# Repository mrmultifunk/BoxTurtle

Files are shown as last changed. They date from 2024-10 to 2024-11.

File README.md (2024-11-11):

# BoxTurtle V1.0
BoxTurtle Automated Filament Changer (requires AFC-Klipper-Add-On (Beta))

BT_Render
Join me on Discord (https://discord.gg/eT8zc3bvPR)

BoxTurtle is exactly what it appears to be — an open source AMS style filament changer for [Klipper](https://klipper3d.org) machines. 
BoxTurtle requires the AFC-Klipper Add-On (found [here](https://github.com/ArmoredTurtle/AFC-Klipper-Add-On)).
The goal of BoxTurtle is to deliver a user experience as close to an AMS as possible in vanilla Klipper. i.e. an "AMS" for any klipperized printer regardless of form factor but [VORON Design](https://vorondesign.com) printers in particular.

If you appreciate the work we are doing, you can support us [here](https://www.armoredturtle.com/pages/donate).

# How it works

BoxTurtle is an automated, lane-based filament changing system, also known by some as a "Type B MMU." Each lane is equipped with its own dedicated motor that moves filament to and from the tool head independently, eliminating the need for a selector cart or servos. Synchronization between the lane motor and the tool head occurs when the filament triggers a sensor (such as [FilaTector](https://github.com/ArmoredTurtle/Filatector)) that is located in or near the tool head.

To accommodate any differences in rotation distance between the extruder in the tool head and the lane motors, BoxTurtle uses a toolhead buffer, such as the [Belay by Annex Engineering](https://github.com/Annex-Engineering/Belay) or the [TurtleNeck](https://github.com/ArmoredTurtle/TurtleNeck) by ArmoredTurtle. This system is "bufferless," meaning no filament boxes (no spaghetti boxes) are required, similar to the AMS. Each lane features an independent respooler equipped with a brushed motor, which helps rewind the spool and assists the lane motor in feeding the filament smoothly. This prevents issues like spool tangling or "bucking."

For precise PWM control of the brushed motors, BoxTurtle relies on a custom MCU, AFC-lite, developed by [Isik's Tech @xbst](https://github.com/xbst/AFC-Lite/)  While the system currently supports BTT MMB CAN, this is a temporary solution to facilitate broader testing and will not be a permanent feature.

# Manual (WIP)

[Will update this as progress is made](https://armoredturtle.xyz)

# Wiring

BoxTurtle_AFC-Lite_Pinout

# Slicer configuration

[Orca Slicer](https://github.com/SoftFever/OrcaSlicer) is the preferred slicer for BoxTurtle use.
## Printer Settings
Orca_Pinter_Settings
## Material Settings
Orca_Material_Settings
## Ramming Settings
Orca_Matterial_Settings

## Printer Machine G-Code
```
M104 S0 ; Stops OS from sending temp waits separately
M140 S0
PRINT_START EXTRUDER=[nozzle_temperature_initial_layer] BED=[bed_temperature_initial_layer_single] Chamber=[chamber_temperature] PRINT_MIN={first_layer_print_min[0]},{first_layer_print_min[1]} PRINT_MAX={first_layer_print_max[0]},{first_layer_print_max[1]} TOOL={initial_tool}
```
## Change Filament G-Code
```
T[next_extruder]
```

## BoxTurtle sourcing/vendors
While BoxTurtle can be mostly self-sourced, some vendors offer partial or full BoxTurtle kits. These vendors also have dedicated channels on the Armored Turtle Discord.

US:
- [DLLPDF](https://dllpdf.com) sells a [BoxTurtle frame kit](http://dllpdf.com/box-turtle-frame)
- [Isik's Tech](https://store.isiks.tech/) has BOM parts, including full kits [here](https://store.isiks.tech/collections/box-turtle-parts). Isik's Tech also ships internationally.
- [Fabreeko](https://www.fabreeko.com/products/box-turtle?_pos=4&_psq=box&_ss=e&_v=1.0)
- [KB3D](https://kb-3d.com/store/boxturtle/2132-pre-order-ldo-box-turtle-automated-filament-changer-kit-v10.html)
- [West3D](https://west3d.com/products/box-turtle-automated-filament-changer-multi-material-unit-by-armored-turtle)
  
EU:
- [Alchemy3D.de](https://alchemy3d.de) has a [BOM in a box kit](https://alchemy3d.de/products/boxturtle)
- [Lab4450.com](https://lab4450.com) resells the [AFC-Lite MCU](https://lab4450.com/product/afc-lite-board/)
- [3DO](https://3do.dk/3d-printer/2942-ldo-boxturtle-afc-kit-til-klipper-printere-forudbestilling.html)

UK:
- [OneTwo3D.co.uk](https://www.onetwo3d.co.uk)
- [Desktop Machine Shop](https://www.desktopmachineshop.com/shop/ldo-boxturtle-afc-kit-v1-0-163?category=4#attribute_values=)
  
AU:
- [DREMC](https://store.dremc.com.au/products/ldo-box-turtle-hardware-kit)
  
## Merch
- BoxTurtle T-Shirt ($3 from each sale goes to support ArmoredTurtle) via [Cotton Bureau](https://cottonbureau.com/p/QKF5XC/shirt/colored-box-turtle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)- also has sweatshirt/hoodie variants
- BoxTurtle Sticker via [Dr. Mursey](https://drmursey.myshopify.com/products/box-turtle)

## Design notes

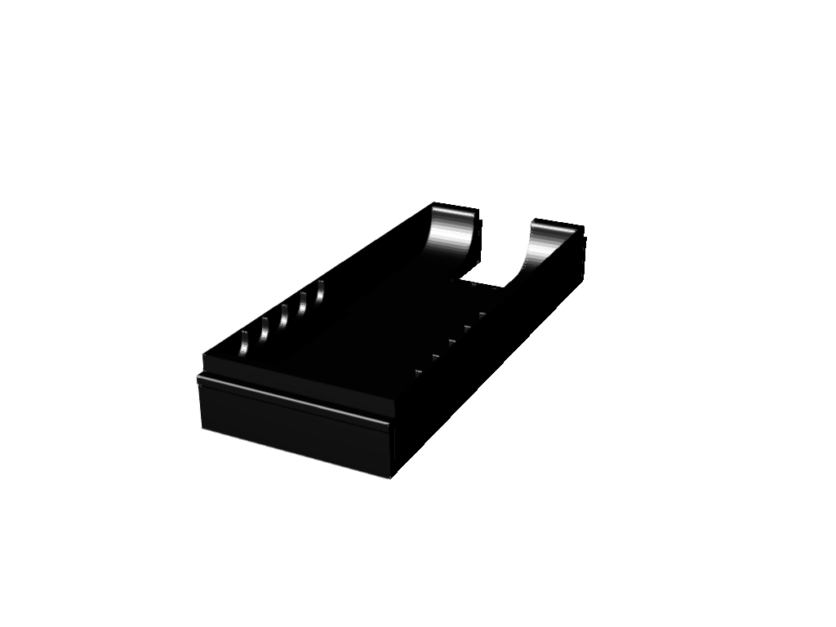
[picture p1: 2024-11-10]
Print_Checklist/images/BoxTurtle/STLs/Trays_(Print_4_of_your_choice)/No_Hardware/tray_plain.stl.png

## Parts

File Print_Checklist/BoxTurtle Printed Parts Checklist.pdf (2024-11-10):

# BoxTurtle Printed Parts Checklist

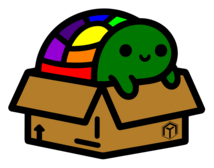
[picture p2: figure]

### Print all of these common parts

STL Preview | Filename | Quantity Needed

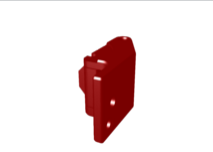
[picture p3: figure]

BoxTurtle/STLs/Extruder/
[a]_guidler_x4.stl (https://github.com/ArmoredTurtle/BoxTurtle/tree/main/STLs/Extruder/[a]_guidler_x4.stl) | 4 ☐☐☐☐

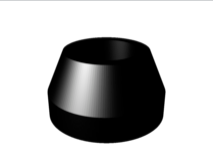
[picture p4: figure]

BoxTurtle/STLs/Frame/
foot_tpu_x4.stl (https://github.com/ArmoredTurtle/BoxTurtle/tree/main/STLs/Frame/foot_tpu_x4.stl) | 4 ☐☐☐☐

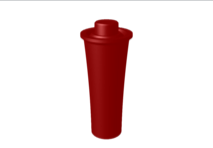
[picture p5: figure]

BoxTurtle/STLs/Idlers/
[a]_idler_roller_x8.stl (https://github.com/ArmoredTurtle/BoxTurtle/tree/main/STLs/Idlers/[a]_idler_roller_x8.stl)

8
☐☐☐☐☐☐☐☐

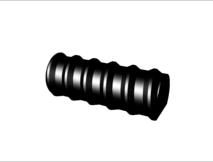
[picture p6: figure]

BoxTurtle/STLs/Idlers/ idler_threaded_joint_x4.stl (https://github.com/ArmoredTurtle/BoxTurtle/tree/main/STLs/Idlers/idler_threaded_joint_x4.stl) | 4 ☐☐☐☐

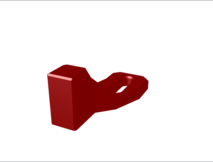
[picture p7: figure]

BoxTurtle/STLs/Respooler/ [a]_feed_trigger_retainer_x4.stl (https://github.com/ArmoredTurtle/BoxTurtle/tree/main/STLs/Respooler/[a]_feed_trigger_retainer_x4.stl) | 4 ☐☐☐☐

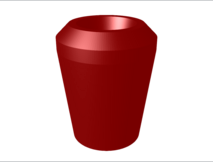
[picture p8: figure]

BoxTurtle/STLs/Respooler/ [a]_feeder_x4.stl (https://github.com/ArmoredTurtle/BoxTurtle/tree/main/STLs/Respooler/[a]_feeder_x4.stl) | 4 ☐☐☐☐
BoxTurtle/STLs/Respooler/ [a]_led_retainer_x4.stl (https://github.com/ArmoredTurtle/BoxTurtle/tree/main/STLs/Respooler/[a]_led_retainer_x4.stl) | 4 ☐☐☐☐
BoxTurtle/STLs/Respooler/ [a]_lightbox_x4.stl (https://github.com/ArmoredTurtle/BoxTurtle/tree/main/STLs/Respooler/[a]_lightbox_x4.stl) | 4 ☐☐☐☐

BoxTurtle/STLs/Respooler/ [a]_wheel_x8.stl (https://github.com/ArmoredTurtle/BoxTurtle/tree/main/STLs/Respooler/[a]_wheel_x8.stl) | 8 ☐☐☐☐☐☐☐☐
BoxTurtle/STLs/Respooler/ [c]_led_diffuser_x4.stl (https://github.com/ArmoredTurtle/BoxTurtle/tree/main/STLs/Respooler/[c]_led_diffuser_x4.stl) | 4 ☐☐☐☐
BoxTurtle/STLs/Respooler/ frame_left_x4.stl (https://github.com/ArmoredTurtle/BoxTurtle/tree/main/STLs/Respooler/frame_left_x4.stl) | 4 ☐☐☐☐
BoxTurtle/STLs/Respooler/ frame_right_x4.stl (https://github.com/ArmoredTurtle/BoxTurtle/tree/main/STLs/Respooler/frame_right_x4.stl) | 4 ☐☐☐☐
BoxTurtle/STLs/Respooler/ gearbox_cover_x4.stl (https://github.com/ArmoredTurtle/BoxTurtle/tree/main/STLs/Respooler/gearbox_cover_x4.stl) | 4 ☐☐☐☐

BoxTurtle/STLs/Respooler/ helical_gear_15_teeth_x4.stl (https://github.com/ArmoredTurtle/BoxTurtle/tree/main/STLs/Respooler/helical_gear_15_teeth_x4.stl) | 4 ☐☐☐☐
BoxTurtle/STLs/Respooler/ helical_gear_30_teeth_x4.stl (https://github.com/ArmoredTurtle/BoxTurtle/tree/main/STLs/Respooler/helical_gear_30_teeth_x4.stl) | 4 ☐☐☐☐
BoxTurtle/STLs/Respooler/ motor_mount_x4.stl (https://github.com/ArmoredTurtle/BoxTurtle/tree/main/STLs/Respooler/motor_mount_x4.stl) | 4 ☐☐☐☐
BoxTurtle/STLs/Respooler/ spur_gear_30_spacer_x4.stl (https://github.com/ArmoredTurtle/BoxTurtle/tree/main/STLs/Respooler/spur_gear_30_spacer_x4.stl) | 4 ☐☐☐☐
BoxTurtle/STLs/Respooler/ tpu_tire_x8.stl (https://github.com/ArmoredTurtle/BoxTurtle/tree/main/STLs/Respooler/tpu_tire_x8.stl) | 8 ☐☐☐☐☐☐☐☐

BoxTurtle/STLs/Respooler/ trigger_x4.stl (https://github.com/ArmoredTurtle/BoxTurtle/tree/main/STLs/Respooler/trigger_x4.stl) | 4 ☐☐☐☐
BoxTurtle/STLs/Skirts/ front_skirt_x2.stl (https://github.com/ArmoredTurtle/BoxTurtle/tree/main/STLs/Skirts/front_skirt_x2.stl) | 2 ☐☐
BoxTurtle/STLs/Skirts/ left_rear_skirt.stl (https://github.com/ArmoredTurtle/BoxTurtle/tree/main/STLs/Skirts/left_rear_skirt.stl) | 1 ☐
BoxTurtle/STLs/Skirts/ right_rear_skirt.stl (https://github.com/ArmoredTurtle/BoxTurtle/tree/main/STLs/Skirts/right_rear_skirt.stl) | 1 ☐

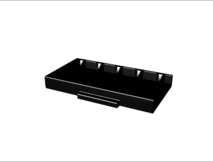
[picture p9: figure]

BoxTurtle/STLs/Skirts/ side_skirt_x4.stl (https://github.com/ArmoredTurtle/BoxTurtle/tree/main/STLs/Skirts/side_skirt_x4.stl) | 4 ☐☐☐☐

BoxTurtle/STLs/
Tools/15t_installation_tool.stl (https://github.com/ArmoredTurtle/BoxTurtle/tree/main/STLs/Tools/15t_installation_tool.stl) | 1 ☐

BoxTurtle/STLs/
Tools/30t_installation_tool.stl (https://github.com/ArmoredTurtle/BoxTurtle/tree/main/STLs/Tools/30t_installation_tool.stl) | 1 ☐

### Electronics Mount (choose one)

STL Preview | Filename | Quantity Needed

BoxTurtle/STLs/Electronics/
afc_mount.stl (https://github.com/ArmoredTurtle/BoxTurtle/tree/main/STLs/Electronics/afc_mount.stl) | 1 ☐

BoxTurtle/STLs/Electronics/
mmb_mount.stl (https://github.com/ArmoredTurtle/BoxTurtle/tree/main/STLs/Electronics/mmb_mount.stl) | 1 ☐

BoxTurtle/STLs/Electronics/
mosfetti_mount.stl (https://github.com/ArmoredTurtle/BoxTurtle/tree/main/STLs/Electronics/mosfetti_mount.stl) | 1 ☐

### Print ONE set of the below two sections, depending on switch type

D2HW-style switches + MR63ZZ bearings

STL Preview | Filename | Quantity Needed
| BoxTurtle/STLs/Extruder/ D2HW_Switch/ extruder_housing_x4.stl (https://github.com/ArmoredTurtle/BoxTurtle/tree/main/STLs/Extruder/D2HW_Switch/extruder_housing_x4.stl)
4 ☐☐☐☐

BoxTurtle/STLs/Extruder/
D2HW_Switch/motor_plate_x4.stl (https://github.com/ArmoredTurtle/BoxTurtle/tree/main/STLs/Extruder/D2HW_Switch/motor_plate_x4.stl) | 4 ☐☐☐☐

BoxTurtle/STLs/Skirts/
[a]_hub_D2HW.stl (if using a hub) (https://github.com/ArmoredTurtle/BoxTurtle/tree/main/STLs/Skirts/[a]_hub_D2HW.stl) | 1 ☐

D2F-style switches + 5mm ball bearings

STL Preview | Filename | Quantity Needed

BoxTurtle/STLs/Extruder/D2F_Switch/
[a]_microswitch_retainer_x4.stl (https://github.com/ArmoredTurtle/BoxTurtle/tree/main/STLs/Extruder/D2F_Switch/[a]_microswitch_retainer_x4.stl) | 4 ☐☐☐☐

BoxTurtle/STLs/Extruder/D2F_Switch/
extruder_housing_x4.stl (https://github.com/ArmoredTurtle/BoxTurtle/tree/main/STLs/Extruder/D2F_Switch/extruder_housing_x4.stl) | 4 ☐☐☐☐

BoxTurtle/STLs/Extruder/D2F_Switch/
motor_plate_x4.stl (https://github.com/ArmoredTurtle/BoxTurtle/tree/main/STLs/Extruder/D2F_Switch/motor_plate_x4.stl) | 4 ☐☐☐☐

BoxTurtle/STLs/Skirts/[a]_hub_D2F.stl
(if using a hub) (https://github.com/ArmoredTurtle/BoxTurtle/tree/main/STLs/Skirts/[a]_hub_D2F.stl) | 1 ☐

### Corners - print ONE set

Corners - Printed (with LEDs)

STL Preview | Filename | Quantity Needed


BoxTurtle/STLs/Frame/
Printed_Corners/[a]_foot_x4.stl (https://github.com/ArmoredTurtle/BoxTurtle/tree/main/STLs/Frame/Printed_Corners/[a]_foot_x4.stl) | 4 ☐☐☐☐

BoxTurtle/STLs/Frame/
Printed_Corners/
[o]_corner_diffuser_x4.stl (https://github.com/ArmoredTurtle/BoxTurtle/tree/main/STLs/Frame/Printed_Corners/[o]_corner_diffuser_x4.stl)

4 ☐☐☐☐

BoxTurtle/STLs/Frame/
Printed_Corners/corner_printed_x4.stl (https://github.com/ArmoredTurtle/BoxTurtle/tree/main/STLs/Frame/Printed_Corners/corner_printed_x4.stl) 4 ☐☐☐☐


BoxTurtle/STLs/Frame/
Printed_Corners/
led_corner_cover_x4.stl (https://github.com/ArmoredTurtle/BoxTurtle/tree/main/STLs/Frame/Printed_Corners/led_corner_cover_x4.stl)

4 ☐☐☐☐


BoxTurtle/STLs/Frame/
Printed_Corners/led_frame_x4.stl (https://github.com/ArmoredTurtle/BoxTurtle/tree/main/STLs/Frame/Printed_Corners/led_frame_x4.stl) | 4 ☐☐☐☐

Corners - Printed (no LEDs)

STL Preview | Filename | Quantity Needed

BoxTurtle/STLs/Frame/
Printed_Corners/[a]_foot_x4.stl (https://github.com/ArmoredTurtle/BoxTurtle/tree/main/STLs/Frame/Printed_Corners/[a]_foot_x4.stl) | 4 ☐☐☐☐

BoxTurtle/STLs/Frame/
Printed_Corners/corner_printed_x4.stl (https://github.com/ArmoredTurtle/BoxTurtle/tree/main/STLs/Frame/Printed_Corners/corner_printed_x4.stl) 4 ☐☐☐☐

BoxTurtle/STLs/Frame/
Printed_Corners/
solid_corner_cover_x4.stl (https://github.com/ArmoredTurtle/BoxTurtle/tree/main/STLs/Frame/Printed_Corners/solid_corner_cover_x4.stl)

4 ☐☐☐☐


100mm 2020 extrusions (uncommon)

STL Preview | Filename | Quantity Needed
| BoxTurtle/STLs/Frame/ Extrusion_Corners/ [a]_foot_extrusion_x4.stl (https://github.com/ArmoredTurtle/BoxTurtle/tree/main/STLs/Frame/Extrusion_Corners/[a]_foot_extrusion_x4.stl)
4 ☐☐☐☐

BoxTurtle/STLs/Frame/
Extrusion_Corners/
corner_cover_extrusion_x4.stl (https://github.com/ArmoredTurtle/BoxTurtle/tree/main/STLs/Frame/Extrusion_Corners/corner_cover_extrusion_x4.stl)

4 ☐☐☐☐

BoxTurtle/STLs/Frame/
Extrusion_Corners/
no_panel_spacer_extrusion_x4.stl (https://github.com/ArmoredTurtle/BoxTurtle/tree/main/STLs/Frame/Extrusion_Corners/no_panel_spacer_extrusion_x4.stl)

4 ☐☐☐☐


### Rear skirts (print one, hub or passthrough)

STL Preview | Filename | Quantity Needed

BoxTurtle/STLs/Skirts/
rear_skirt_center_hub.stl (https://github.com/ArmoredTurtle/BoxTurtle/tree/main/STLs/Skirts/rear_skirt_center_hub.stl) | 1 ☐

BoxTurtle/STLs/Skirts/
rear_skirt_center_passthrough.stl (https://github.com/ArmoredTurtle/BoxTurtle/tree/main/STLs/Skirts/rear_skirt_center_passthrough.stl) | 1 ☐

### Trays - No Hardware (235mm or larger build plates) - print one set (if build plate allows)

No Hardware - Desiccant

STL Preview | Filename | Quantity Needed
| BoxTurtle/STLs/ Trays_(Print_4_of_your_choice)/ No_Hardware/tray_desiccant.stl (https://github.com/ArmoredTurtle/BoxTurtle/tree/main/STLs/Trays_(Print_4_of_your_choice)/No_Hardware/tray_desiccant.stl)
4 ☐☐☐☐


No Hardware - Inlay

STL Preview | Filename | Quantity Needed
| BoxTurtle/STLs/ Trays_(Print_4_of_your_choice)/ No_Hardware/tray_inlay.stl (https://github.com/ArmoredTurtle/BoxTurtle/tree/main/STLs/Trays_(Print_4_of_your_choice)/No_Hardware/tray_inlay.stl)
4 ☐☐☐☐

BoxTurtle/STLs/
Trays_(Print_4_of_your_choice)/ [a]_logo_inlay.stl (https://github.com/ArmoredTurtle/BoxTurtle/blob/main/STLs/Trays_(Print_4_of_your_choice)/%5Ba%5D_logo_inlay.stl)

4 ☐☐☐☐

No Hardware - Multicolor

STL Preview | Filename | Quantity Needed
| BoxTurtle/STLs/ Trays_(Print_4_of_your_choice)/ No_Hardware/tray_multicolor.stl (https://github.com/ArmoredTurtle/BoxTurtle/tree/main/STLs/Trays_(Print_4_of_your_choice)/No_Hardware/tray_multicolor.stl)
4 ☐☐☐☐


No Hardware - Plain

STL Preview | Filename | Quantity Needed
| BoxTurtle/STLs/ Trays_(Print_4_of_your_choice)/ No_Hardware/tray_plain.stl (https://github.com/ArmoredTurtle/BoxTurtle/tree/main/STLs/Trays_(Print_4_of_your_choice)/No_Hardware/tray_plain.stl)
4 ☐☐☐☐

### Trays - Hardware (> 220mm but <235mm build plates) - print one set (if build plate does not allow for no hardware)

Hardware - All

STL Preview | Filename | Quantity Needed
| BoxTurtle/STLs/ Trays_(Print_4_of_your_choice)/ W_Hardware/bar_long_x4.stl (https://github.com/ArmoredTurtle/BoxTurtle/tree/main/STLs/Trays_(Print_4_of_your_choice)/W_Hardware/bar_long_x4.stl)
4 ☐☐☐☐

BoxTurtle/STLs/
Trays_(Print_4_of_your_choice)/ W_Hardware/bar_short_x8.stl (https://github.com/ArmoredTurtle/BoxTurtle/tree/main/STLs/Trays_(Print_4_of_your_choice)/W_Hardware/bar_short_x8.stl)

8
☐☐☐☐☐☐☐☐

Hardware - Desiccant

STL Preview | Filename | Quantity Needed
| BoxTurtle/STLs/ Trays_(Print_4_of_your_choice)/ W_Hardware/hw_tray_desiccant.stl (https://github.com/ArmoredTurtle/BoxTurtle/tree/main/STLs/Trays_(Print_4_of_your_choice)/W_Hardware/hw_tray_desiccant.stl) | 1 ☐

Hardware - Inlay

STL Preview | Filename | Quantity Needed


| BoxTurtle/STLs/ Trays_(Print_4_of_your_choice)/ W_Hardware/hw_tray_inlay.stl (https://github.com/ArmoredTurtle/BoxTurtle/tree/main/STLs/Trays_(Print_4_of_your_choice)/W_Hardware/hw_tray_inlay.stl) | 1 ☐

BoxTurtle/STLs/
Trays_(Print_4_of_your_choice)/ [a]_logo_inlay.stl (https://github.com/ArmoredTurtle/BoxTurtle/blob/main/STLs/Trays_(Print_4_of_your_choice)/%5Ba%5D_logo_inlay.stl)

4 ☐☐☐☐


Hardware - Multicolor

STL Preview | Filename | Quantity Needed
| BoxTurtle/STLs/ Trays_(Print_4_of_your_choice)/ W_Hardware/hw_tray_multicolor.stl (https://github.com/ArmoredTurtle/BoxTurtle/tree/main/STLs/Trays_(Print_4_of_your_choice)/W_Hardware/hw_tray_multicolor.stl)
4 ☐☐☐☐

Hardware - Plain

STL Preview | Filename | Quantity Needed
| BoxTurtle/STLs/ Trays_(Print_4_of_your_choice)/ W_Hardware/hw_tray_plain.stl (https://github.com/ArmoredTurtle/BoxTurtle/tree/main/STLs/Trays_(Print_4_of_your_choice)/W_Hardware/hw_tray_plain.stl)
4 ☐☐☐☐


### Desiccant Boxes (print 4 lids + 4 of one size, if using)

STL Preview | Filename | Quantity Needed


| BoxTurtle/STLs/ Trays_(Print_4_of_your_choice)/ desiccant_case_18mm_x4.stl (https://github.com/ArmoredTurtle/BoxTurtle/tree/main/STLs/Trays_(Print_4_of_your_choice)/desiccant_case_18mm_x4.stl)
4 ☐☐☐☐


BoxTurtle/STLs/
Trays_(Print_4_of_your_choice)/ desiccant_case_28mm_x4.stl (https://github.com/ArmoredTurtle/BoxTurtle/tree/main/STLs/Trays_(Print_4_of_your_choice)/desiccant_case_28mm_x4.stl)

4 ☐☐☐☐


BoxTurtle/STLs/
Trays_(Print_4_of_your_choice)/ desiccant_lid_solid_x4.stl (print using modifier shape) (https://github.com/ArmoredTurtle/BoxTurtle/tree/main/STLs/Trays_(Print_4_of_your_choice)/desiccant_lid_solid_x4.stl)

4 ☐☐☐☐

### Optional parts

BoxTurtle Parts - TurtleNeck Buffer (optional)

STL Preview | Filename | Quantity Needed
BoxTurtle/STLs/Buffer/Frame.stl (https://github.com/ArmoredTurtle/BoxTurtle/tree/main/STLs/Buffer/Frame.stl) | 1 ☐

BoxTurtle/STLs/Buffer/
[a]_slide.stl (https://github.com/ArmoredTurtle/BoxTurtle/tree/main/STLs/Buffer/[a]_slide.stl) | 1 ☐
BoxTurtle/STLs/Buffer/lid.stl (https://github.com/ArmoredTurtle/BoxTurtle/tree/main/STLs/Buffer/lid.stl) | 1 ☐

Top-mount legs for stock Voron printers (optional) - print one set of 4 for your printer size

STL Preview | Filename | Quantity Needed


BoxTurtle/STLs/Mounts/
turtle_leg_250_x4.stl (https://github.com/ArmoredTurtle/BoxTurtle/tree/main/STLs/Mounts/turtle_leg_250_x4.stl) | 4 ☐☐☐☐


BoxTurtle/STLs/Mounts/
turtle_leg_300_x4.stl (https://github.com/ArmoredTurtle/BoxTurtle/tree/main/STLs/Mounts/turtle_leg_300_x4.stl) | 4 ☐☐☐☐


BoxTurtle/STLs/Mounts/
turtle_leg_350_x4.stl (https://github.com/ArmoredTurtle/BoxTurtle/tree/main/STLs/Mounts/turtle_leg_350_x4.stl) | 4 ☐☐☐☐

### Bottom panel (optional)

STL Preview | Filename | Quantity Needed

BoxTurtle/STLs/Frame/
bottom_panel_3mm_abs.stl (https://github.com/ArmoredTurtle/BoxTurtle/tree/main/STLs/Frame/bottom_panel_3mm_abs.stl) | 1 ☐

BoxTurtle/STLs/Frame/
panel_spacer_x4.stl (if needed, scale in Z as appropriate) (https://github.com/ArmoredTurtle/BoxTurtle/tree/main/STLs/Frame/panel_spacer_x4.stl)

4 ☐☐☐☐

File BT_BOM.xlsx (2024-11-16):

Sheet: Sheet
Category | Item | Quantity | Notes | Links
Frame | 360mm 2020 extrusion | 4 | HFSB5-2020-360-TPW
Frame | 220mm 2020 extrusion | 4 | HFSB5-2020-220-TPW
Electronics | NEMA14 10 tooth pancake stepper | 4 |  | https://www.aliexpress.us/item/3256804884302626.html
Electronics | AFC-Lite Board | 1 |  | https://store.isiks.tech/products/afc-lite
Electronics | TMC2209/2226 Drivers | 4
Electronics | RGBW LED PCB (WS2812) | 4 |  | https://www.aliexpress.us/item/3256801785673787.html
Electronics | 3010 axial fan 5v | 1 |  | https://www.aliexpress.us/item/3256802884825067.html
Electronics | N20 6v/500RPM motors | 4 |  | https://www.aliexpress.us/item/2251832836005412.html
Electronics | D2F W/Lever | 4
Electronics | D2HW-C201H | 5
Bearings | MR63ZZ bearing | 13 |  | https://www.aliexpress.us/item/3256801934742685.html
Bearings | MR148ZZ bearing | 16 |  | https://www.aliexpress.us/item/2251832648440163.html
M2 hardware | M2x10 self tapping screws | 12
M3 Hardware | M3x30 BHCS | 4
M3 Hardware | M3x16 BHCS | 4
M3 Hardware | M3x6 SHCS | 8
M3 Hardware | M3x8 SHCS | 78
M3 Hardware | M3x10 SHCS | 16
M3 Hardware | M3 threaded insert | 70
M3 Hardware | M3 washer | 8
M5 Hardware | M5x16 BHCS | 20
M5 Hardware | M5 washer | 4
M5 Hardware | M5 hex nut | 4 | For printed corners
Misc hardware | 8x80 shaft | 4 |  | https://www.aliexpress.us/item/2255800287548941.html
Misc hardware | BMG gear kit | 4 |  | https://www.aliexpress.us/item/3256805442986544.html
Misc hardware | 6x3 magnet | 8
Misc hardware | ECAS04 Bowden coupler | 20 |  | https://www.aliexpress.us/item/3256806432021232.html
Misc hardware | PG7 Cable Strain Relief | 1
Misc hardware | M3 roll nuts | 2
Bowden Tube | 4mm OD 3mm ID | ~.5M
Bowden Tube | 4mm OD 2mm ID | ~3M
For TN Buffer | D2F W/Lever | 2
For TN Buffer | M2x10 Self Tappers | 4
For TN Buffer | M3x8 SHCS | 4
For TN Buffer | M3 threaded inserts | 4
For TN Buffer | ECAS04 bowden coupler | 2
BT Hard Mounts | M3 Roll nuts | 12
BT Hard Mounts | M3x10 SHCS | 12

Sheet: For E-Spooler
Category | Item | Quantity pr E-spooler | Notes | Links | Total amount | Price | Total | Number of E-spools to be built | 12
Electronics | N20 6v/500RPM motors | 1 |  | https://www.aliexpress.us/item/2251832836005412.html | 12 | 16 kr. | 192 kr.
Electronics | M2X10 SHCS | 2 | Normal thread or selfcutting |  | 24
Electronics | D2F Straight Microswitch | 1 | 01L (With lever) | https://www.aliexpress.us/item/4000071338221.html | 12 | 110 kr. | 110 kr.
Electronics | DRV8833 Motor Controller |  |  | https://www.aliexpress.us/item/1005006282457232.html | 8 | 42 kr. | 42 kr.
Electronics | RGBW LED PCB | 1 |  | https://www.aliexpress.us/item/1005001971988539.html | 12 | 60 kr. | 60 kr.
Hardware | M3X8 BHCS | 2 |  |  | 24
Hardware | M3X6 BHCS | 2 |  |  | 24
Hardware | M5X12 SHCS | 1 |  |  | 12
Hardware | M3X25 SHCS | 2 |  |  | 24
Hardware | M3X10 SHCS | 4 |  |  | 48
Hardware | M3X8 SHCS | 5 |  |  | 60
Hardware | M3 Heat Set Insert | 7 |  | https://www.aliexpress.us/item/1005002897983868.html | 84 | 32 kr. | 32 kr.
Hardware | ECAS Bowden Collet | 1 | ECAS04 Bowden coupler | https://www.aliexpress.us/item/3256806432021232.html | 12 | 45 kr. | 45 kr.
Hardware | 6X3 magnet | 2 |  | https://www.aliexpress.us/item/1005006291065081.html | 24 | 32 kr. | 32 kr.
Hardware | M8X80 Shaft | 1 |  | https://www.aliexpress.us/item/2255800287548941.html | 12 | 78 kr. | 78 kr.
Hardware | M3 T-nut | 2 |  | https://www.aliexpress.us/item/1005003678960619.html | 24 | 55 kr. | 55 kr.
Hardware | M5 T-Nut | 1 |  | https://www.aliexpress.us/item/1005003678960619.html | 12 | 44 kr. | 44 kr.
Hardware | 2020 T Slot extrusion |  | 400mm | https://www.aliexpress.us/item/1005003428294239.html | 4 | 135 kr. | 135 kr.
Bearings | MR148 | 2 |  | https://www.aliexpress.us/item/2251832648440163.html | 24 | 30 kr. | 90 kr.
Bearings | MR63 | 2 |  | https://www.aliexpress.us/item/3256801934742685.html | 24 | 24 kr. | 72 kr.
Total |  |  |  |  |  |  | 987 kr.

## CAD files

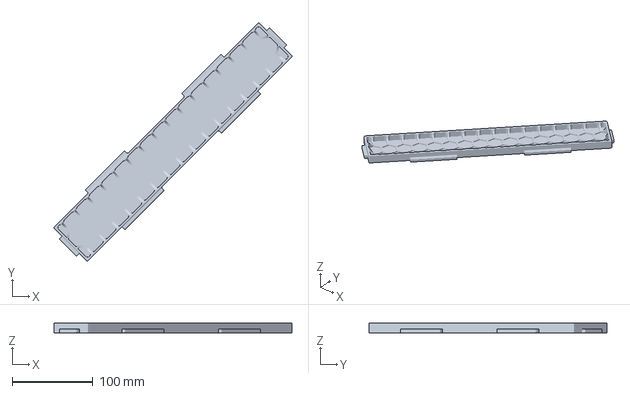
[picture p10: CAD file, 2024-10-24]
STLs/Skirts/Mesh_Skirt_Project_Files/front_skirt_full.3mf
295.2 x 295.2 x 12.5 mm

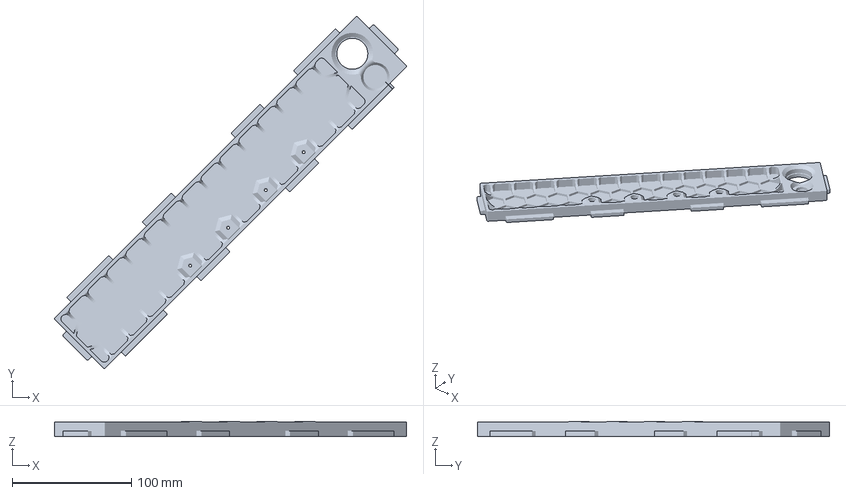
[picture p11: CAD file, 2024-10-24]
STLs/Skirts/Mesh_Skirt_Project_Files/rear_skirt_passthrough_full.3mf
295.7 x 295.7 x 13.0 mm

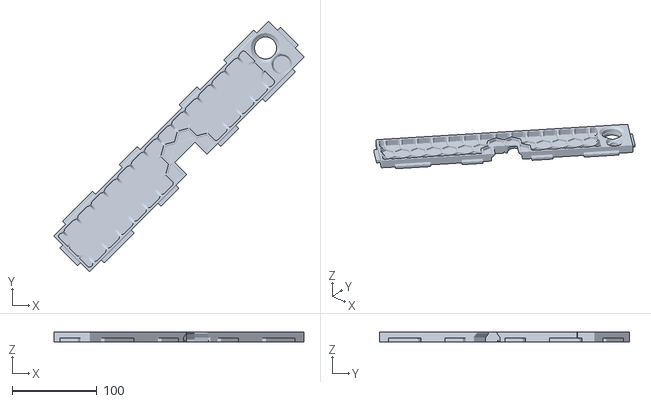
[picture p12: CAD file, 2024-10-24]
STLs/Skirts/One_Piece_Skirts/rear_skirt_hub_full.stl
295.7 x 295.7 x 12.4

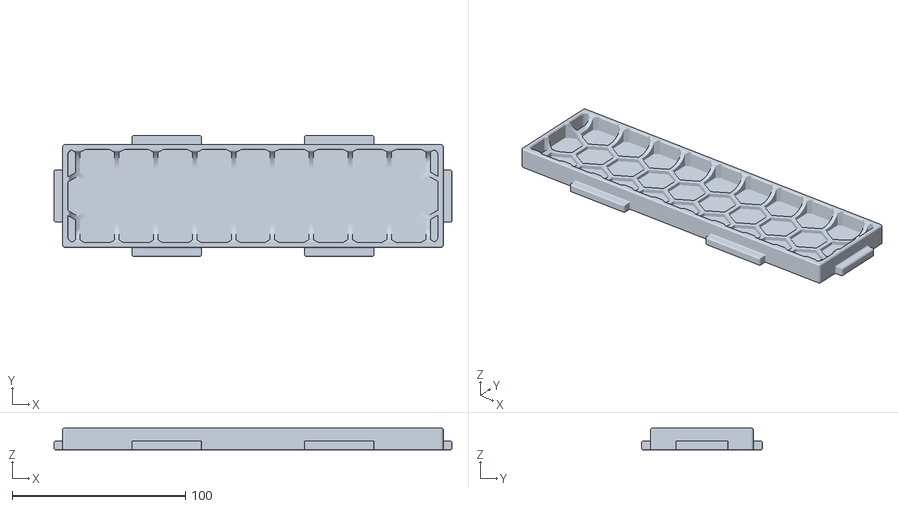
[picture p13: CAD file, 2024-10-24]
STLs/Skirts/One_Piece_Skirts/side_skirt_full.stl
229.6 x 69.6 x 12.5

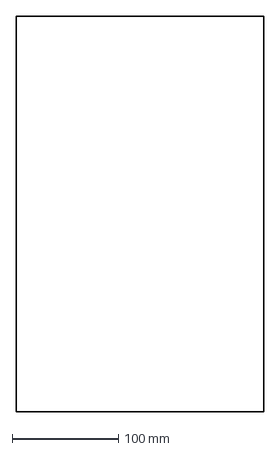
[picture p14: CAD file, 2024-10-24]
CAD/box_turtle_enclosure_top.dxf
232.4 x 372.0 mm

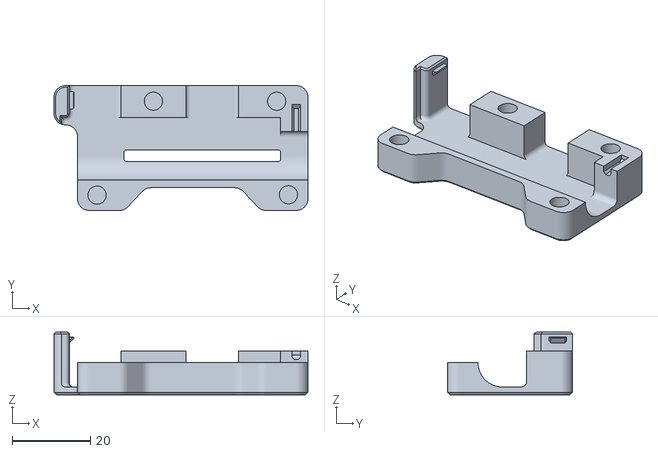
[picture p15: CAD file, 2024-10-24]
STLs/Buffer/lid.stl
64.9 x 31.9 x 16.0

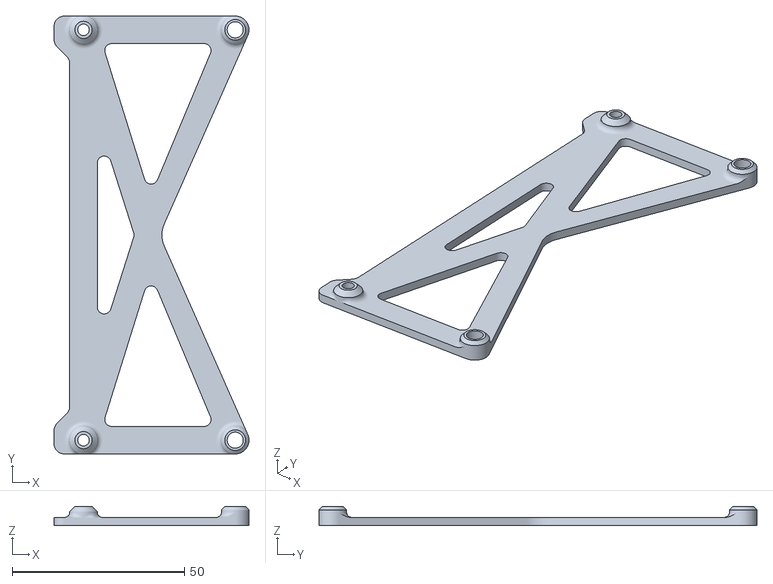
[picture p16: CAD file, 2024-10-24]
STLs/Electronics/mmb_mount.stl
56.6 x 127.0 x 5.59

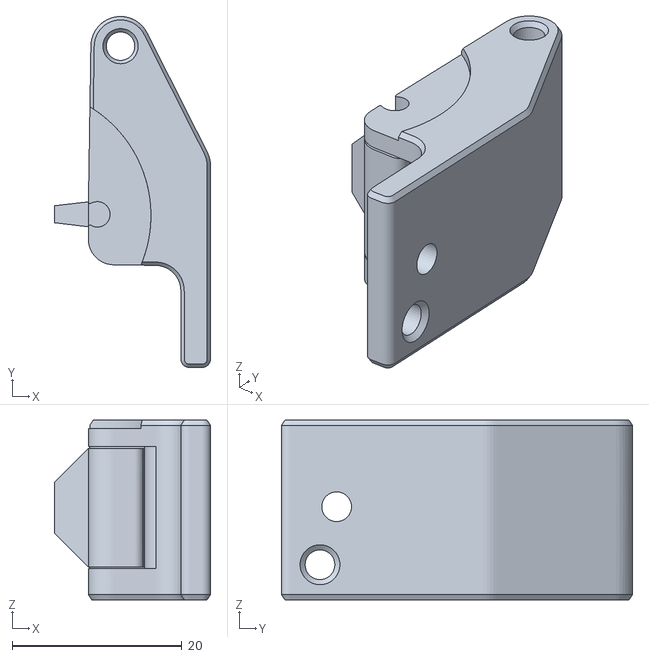
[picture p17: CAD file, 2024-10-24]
STLs/Extruder/[a]_guidler_x4.stl
18.4 x 41.4 x 21.2

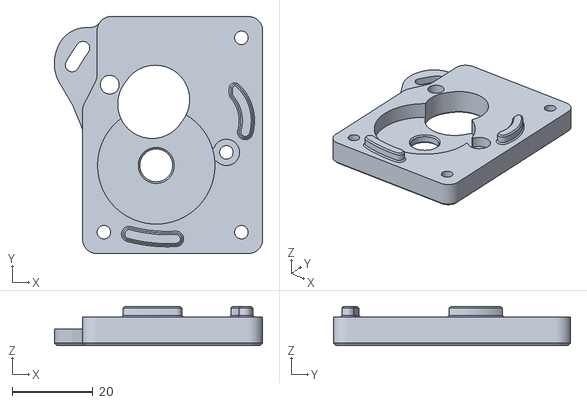
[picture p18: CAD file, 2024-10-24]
STLs/Extruder/D2F_Switch/motor_plate_x4.stl
51.5 x 58.6 x 9.65

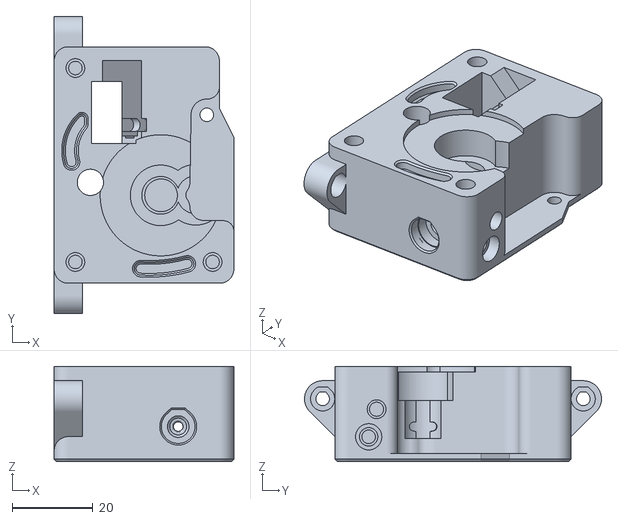
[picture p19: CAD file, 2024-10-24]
STLs/Extruder/D2HW_Switch/extruder_housing_x4.stl
44.5 x 73.6 x 23.6

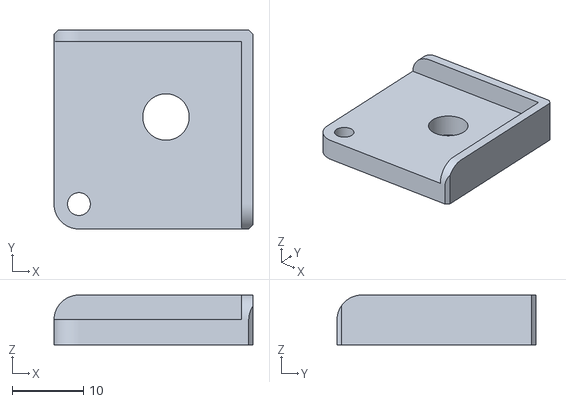
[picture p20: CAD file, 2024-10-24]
STLs/Frame/Extrusion_Corners/[a]_foot_extrusion_x4.stl
27.9 x 27.9 x 7.00

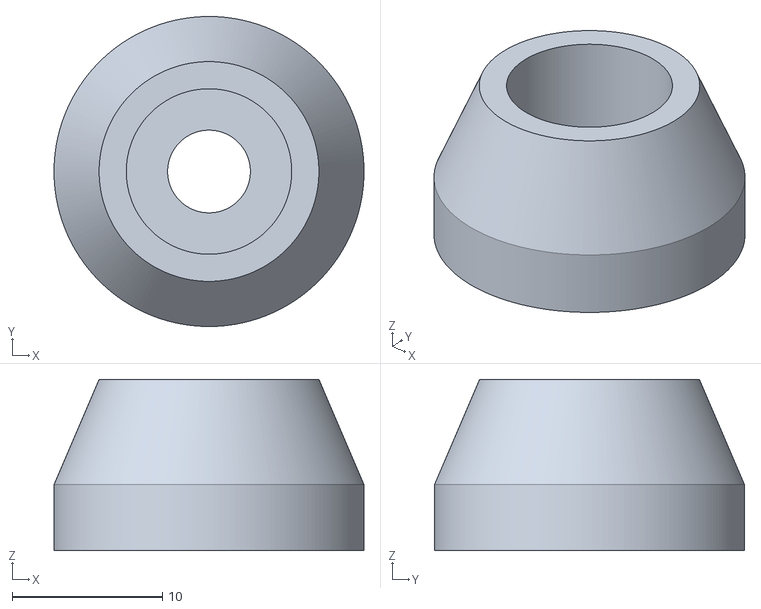
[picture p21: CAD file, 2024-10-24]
STLs/Frame/foot_tpu_x4.stl
20.6 x 20.6 x 11.4

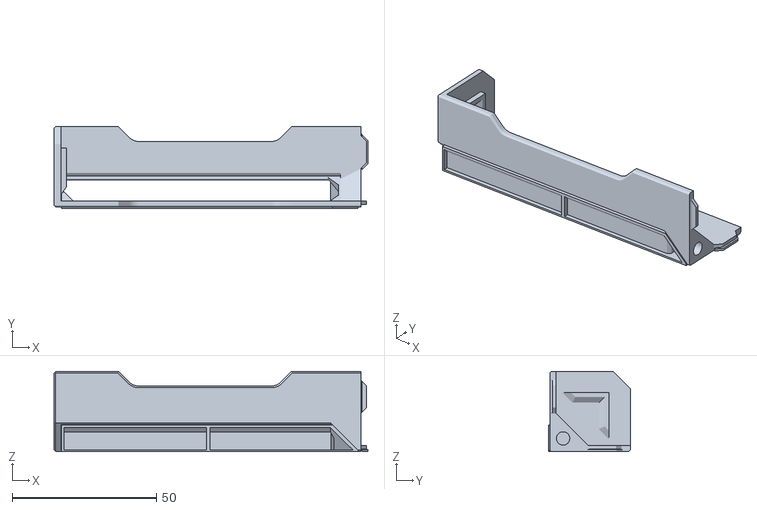
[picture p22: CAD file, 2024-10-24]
STLs/Frame/Printed_Corners/led_corner_cover_x4.stl
108.9 x 28.3 x 27.9

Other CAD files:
STLs/Skirts/One_Piece_Skirts/front_skirt_full.stl
CAD/Box Turtle Assembled.step
STLs/Skirts/One_Piece_Skirts/rear_skirt_passthrough_full.stl
STLs/Skirts/Mesh_Skirt_Project_Files/side_skirt_full.3mf
STLs/Skirts/Mesh_Skirt_Project_Files/rear_skirt_hub_full.3mf
CAD/Box Turtle Assembled.f3z
CAD/Box Turtle Simplified.step
CAD/box_turtle_bottom_panel.dxf
CAD/box_turtle_enclosure_front_rear_x2.dxf
CAD/box_turtle_enclosure_sides_x2.dxf
STLs/Buffer/Frame.stl
STLs/Buffer/[a]_slide.stl
STLs/Electronics/afc_mount.stl
STLs/Electronics/mosfetti_mount.stl
STLs/Extruder/D2F_Switch/[a]_microswitch_retainer_x4.stl
STLs/Extruder/D2F_Switch/extruder_housing_x4.stl
STLs/Extruder/D2HW_Switch/motor_plate_x4.stl
STLs/Frame/Extrusion_Corners/corner_cover_extrusion_x4.stl
STLs/Frame/Extrusion_Corners/no_panel_spacer_extrusion_x4.stl
STLs/Frame/Printed_Corners/[a]_foot_x4.stl
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

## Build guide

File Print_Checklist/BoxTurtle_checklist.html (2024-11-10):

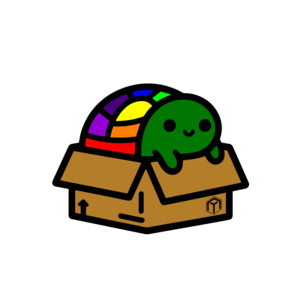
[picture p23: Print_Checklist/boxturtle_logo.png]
(BoxTurtle logo)
 | BoxTurtle Printed Parts Checklist

## Print all of these common parts

STL Preview | Filename | Quantity Needed
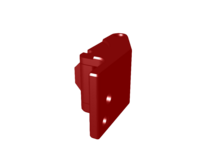
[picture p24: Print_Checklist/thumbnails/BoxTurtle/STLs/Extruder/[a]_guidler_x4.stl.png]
 | BoxTurtle/STLs/Extruder/[a]_guidler_x4.stl (https://github.com/ArmoredTurtle/BoxTurtle/tree/main/STLs/Extruder/[a]_guidler_x4.stl) | 4 ☐☐☐☐
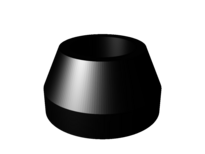
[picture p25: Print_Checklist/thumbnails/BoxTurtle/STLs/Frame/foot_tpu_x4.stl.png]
 | BoxTurtle/STLs/Frame/foot_tpu_x4.stl (https://github.com/ArmoredTurtle/BoxTurtle/tree/main/STLs/Frame/foot_tpu_x4.stl) | 4 ☐☐☐☐
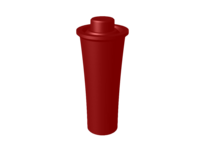
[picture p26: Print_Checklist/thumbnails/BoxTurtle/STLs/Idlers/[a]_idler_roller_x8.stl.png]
 | BoxTurtle/STLs/Idlers/[a]_idler_roller_x8.stl (https://github.com/ArmoredTurtle/BoxTurtle/tree/main/STLs/Idlers/[a]_idler_roller_x8.stl) | 8 ☐☐☐☐☐☐☐☐
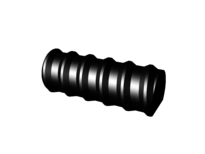
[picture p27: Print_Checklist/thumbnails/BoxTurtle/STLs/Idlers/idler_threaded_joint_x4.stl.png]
 | BoxTurtle/STLs/Idlers/idler_threaded_joint_x4.stl (https://github.com/ArmoredTurtle/BoxTurtle/tree/main/STLs/Idlers/idler_threaded_joint_x4.stl) | 4 ☐☐☐☐
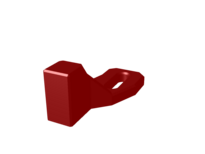
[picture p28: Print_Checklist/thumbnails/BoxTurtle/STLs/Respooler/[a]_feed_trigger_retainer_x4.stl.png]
 | BoxTurtle/STLs/Respooler/[a]_feed_trigger_retainer_x4.stl (https://github.com/ArmoredTurtle/BoxTurtle/tree/main/STLs/Respooler/[a]_feed_trigger_retainer_x4.stl) | 4 ☐☐☐☐
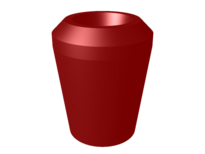
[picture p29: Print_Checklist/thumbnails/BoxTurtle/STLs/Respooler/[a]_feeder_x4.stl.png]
 | BoxTurtle/STLs/Respooler/[a]_feeder_x4.stl (https://github.com/ArmoredTurtle/BoxTurtle/tree/main/STLs/Respooler/[a]_feeder_x4.stl) | 4 ☐☐☐☐
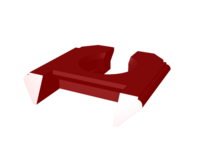
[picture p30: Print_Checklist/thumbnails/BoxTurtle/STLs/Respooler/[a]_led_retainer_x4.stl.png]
 | BoxTurtle/STLs/Respooler/[a]_led_retainer_x4.stl (https://github.com/ArmoredTurtle/BoxTurtle/tree/main/STLs/Respooler/[a]_led_retainer_x4.stl) | 4 ☐☐☐☐
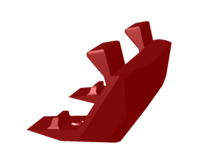
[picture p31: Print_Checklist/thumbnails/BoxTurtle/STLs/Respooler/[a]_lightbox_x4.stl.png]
 | BoxTurtle/STLs/Respooler/[a]_lightbox_x4.stl (https://github.com/ArmoredTurtle/BoxTurtle/tree/main/STLs/Respooler/[a]_lightbox_x4.stl) | 4 ☐☐☐☐
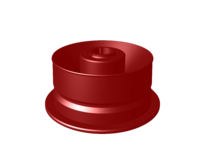
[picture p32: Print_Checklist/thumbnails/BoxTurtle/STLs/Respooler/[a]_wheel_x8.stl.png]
 | BoxTurtle/STLs/Respooler/[a]_wheel_x8.stl (https://github.com/ArmoredTurtle/BoxTurtle/tree/main/STLs/Respooler/[a]_wheel_x8.stl) | 8 ☐☐☐☐☐☐☐☐
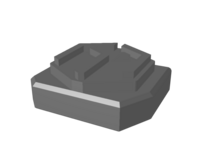
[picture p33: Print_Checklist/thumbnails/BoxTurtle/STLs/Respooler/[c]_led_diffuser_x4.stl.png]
 | BoxTurtle/STLs/Respooler/[c]_led_diffuser_x4.stl (https://github.com/ArmoredTurtle/BoxTurtle/tree/main/STLs/Respooler/[c]_led_diffuser_x4.stl) | 4 ☐☐☐☐
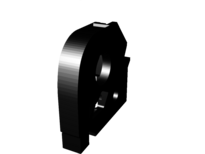
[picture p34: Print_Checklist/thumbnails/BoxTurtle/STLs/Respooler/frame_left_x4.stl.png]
 | BoxTurtle/STLs/Respooler/frame_left_x4.stl (https://github.com/ArmoredTurtle/BoxTurtle/tree/main/STLs/Respooler/frame_left_x4.stl) | 4 ☐☐☐☐
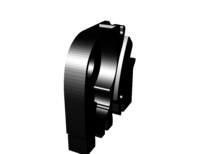
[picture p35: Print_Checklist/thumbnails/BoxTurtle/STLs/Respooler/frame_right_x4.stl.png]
 | BoxTurtle/STLs/Respooler/frame_right_x4.stl (https://github.com/ArmoredTurtle/BoxTurtle/tree/main/STLs/Respooler/frame_right_x4.stl) | 4 ☐☐☐☐
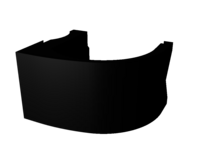
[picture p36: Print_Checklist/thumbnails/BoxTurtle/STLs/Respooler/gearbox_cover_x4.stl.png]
 | BoxTurtle/STLs/Respooler/gearbox_cover_x4.stl (https://github.com/ArmoredTurtle/BoxTurtle/tree/main/STLs/Respooler/gearbox_cover_x4.stl) | 4 ☐☐☐☐
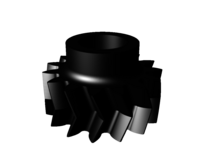
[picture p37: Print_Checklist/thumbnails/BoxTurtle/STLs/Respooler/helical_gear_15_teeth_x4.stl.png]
 | BoxTurtle/STLs/Respooler/helical_gear_15_teeth_x4.stl (https://github.com/ArmoredTurtle/BoxTurtle/tree/main/STLs/Respooler/helical_gear_15_teeth_x4.stl) | 4 ☐☐☐☐
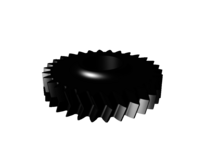
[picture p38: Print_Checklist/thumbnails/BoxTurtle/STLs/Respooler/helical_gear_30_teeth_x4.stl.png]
 | BoxTurtle/STLs/Respooler/helical_gear_30_teeth_x4.stl (https://github.com/ArmoredTurtle/BoxTurtle/tree/main/STLs/Respooler/helical_gear_30_teeth_x4.stl) | 4 ☐☐☐☐
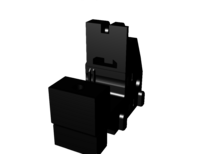
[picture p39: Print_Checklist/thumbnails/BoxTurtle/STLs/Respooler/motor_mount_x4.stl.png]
 | BoxTurtle/STLs/Respooler/motor_mount_x4.stl (https://github.com/ArmoredTurtle/BoxTurtle/tree/main/STLs/Respooler/motor_mount_x4.stl) | 4 ☐☐☐☐
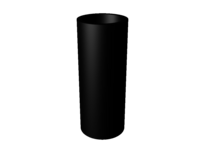
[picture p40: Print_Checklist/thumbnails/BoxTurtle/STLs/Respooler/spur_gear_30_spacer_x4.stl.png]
 | BoxTurtle/STLs/Respooler/spur_gear_30_spacer_x4.stl (https://github.com/ArmoredTurtle/BoxTurtle/tree/main/STLs/Respooler/spur_gear_30_spacer_x4.stl) | 4 ☐☐☐☐
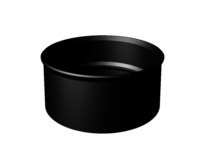
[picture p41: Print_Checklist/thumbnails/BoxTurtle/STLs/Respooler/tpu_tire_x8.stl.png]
 | BoxTurtle/STLs/Respooler/tpu_tire_x8.stl (https://github.com/ArmoredTurtle/BoxTurtle/tree/main/STLs/Respooler/tpu_tire_x8.stl) | 8 ☐☐☐☐☐☐☐☐
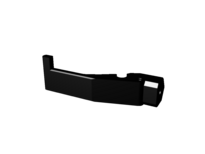
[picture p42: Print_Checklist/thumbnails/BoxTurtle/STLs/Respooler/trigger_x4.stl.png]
 | BoxTurtle/STLs/Respooler/trigger_x4.stl (https://github.com/ArmoredTurtle/BoxTurtle/tree/main/STLs/Respooler/trigger_x4.stl) | 4 ☐☐☐☐
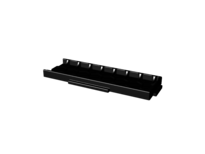
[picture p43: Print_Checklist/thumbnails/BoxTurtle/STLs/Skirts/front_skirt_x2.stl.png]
 | BoxTurtle/STLs/Skirts/front_skirt_x2.stl (https://github.com/ArmoredTurtle/BoxTurtle/tree/main/STLs/Skirts/front_skirt_x2.stl) | 2 ☐☐
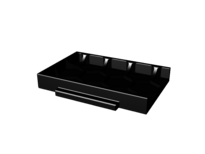
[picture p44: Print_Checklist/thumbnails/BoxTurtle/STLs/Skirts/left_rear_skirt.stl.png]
 | BoxTurtle/STLs/Skirts/left_rear_skirt.stl (https://github.com/ArmoredTurtle/BoxTurtle/tree/main/STLs/Skirts/left_rear_skirt.stl) | 1 ☐
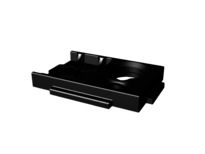
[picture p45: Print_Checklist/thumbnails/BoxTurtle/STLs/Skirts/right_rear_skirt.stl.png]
 | BoxTurtle/STLs/Skirts/right_rear_skirt.stl (https://github.com/ArmoredTurtle/BoxTurtle/tree/main/STLs/Skirts/right_rear_skirt.stl) | 1 ☐
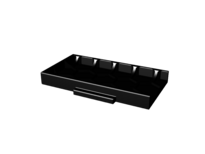
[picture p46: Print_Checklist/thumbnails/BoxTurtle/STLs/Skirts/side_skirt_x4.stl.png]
 | BoxTurtle/STLs/Skirts/side_skirt_x4.stl (https://github.com/ArmoredTurtle/BoxTurtle/tree/main/STLs/Skirts/side_skirt_x4.stl) | 4 ☐☐☐☐
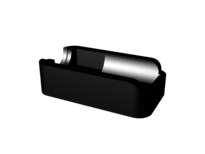
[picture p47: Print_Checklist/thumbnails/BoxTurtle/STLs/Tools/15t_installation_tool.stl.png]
 | BoxTurtle/STLs/Tools/15t_installation_tool.stl (https://github.com/ArmoredTurtle/BoxTurtle/tree/main/STLs/Tools/15t_installation_tool.stl) | 1 ☐
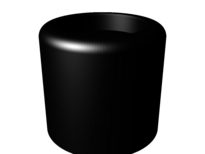
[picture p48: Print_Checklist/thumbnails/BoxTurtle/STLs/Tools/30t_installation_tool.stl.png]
 | BoxTurtle/STLs/Tools/30t_installation_tool.stl (https://github.com/ArmoredTurtle/BoxTurtle/tree/main/STLs/Tools/30t_installation_tool.stl) | 1 ☐

## Electronics Mount (choose one)

STL Preview | Filename | Quantity Needed
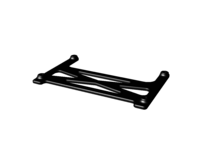
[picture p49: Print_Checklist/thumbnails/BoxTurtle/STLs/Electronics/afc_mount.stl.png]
 | BoxTurtle/STLs/Electronics/afc_mount.stl (https://github.com/ArmoredTurtle/BoxTurtle/tree/main/STLs/Electronics/afc_mount.stl) | 1 ☐
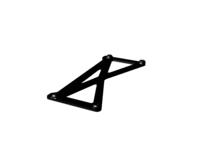
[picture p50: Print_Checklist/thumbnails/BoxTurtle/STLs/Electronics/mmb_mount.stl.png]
 | BoxTurtle/STLs/Electronics/mmb_mount.stl (https://github.com/ArmoredTurtle/BoxTurtle/tree/main/STLs/Electronics/mmb_mount.stl) | 1 ☐
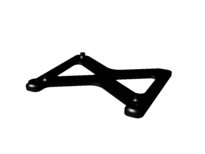
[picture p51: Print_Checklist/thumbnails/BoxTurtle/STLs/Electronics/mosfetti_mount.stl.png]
 | BoxTurtle/STLs/Electronics/mosfetti_mount.stl (https://github.com/ArmoredTurtle/BoxTurtle/tree/main/STLs/Electronics/mosfetti_mount.stl) | 1 ☐

## Print ONE set of the below two sections, depending on switch type

### D2HW-style switches + MR63ZZ bearings

STL Preview | Filename | Quantity Needed
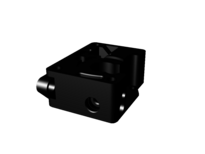
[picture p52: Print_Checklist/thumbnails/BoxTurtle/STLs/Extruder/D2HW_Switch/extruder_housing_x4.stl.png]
 | BoxTurtle/STLs/Extruder/D2HW_Switch/extruder_housing_x4.stl (https://github.com/ArmoredTurtle/BoxTurtle/tree/main/STLs/Extruder/D2HW_Switch/extruder_housing_x4.stl) | 4 ☐☐☐☐
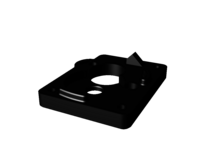
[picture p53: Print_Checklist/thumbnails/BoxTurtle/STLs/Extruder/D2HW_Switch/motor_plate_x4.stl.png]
 | BoxTurtle/STLs/Extruder/D2HW_Switch/motor_plate_x4.stl (https://github.com/ArmoredTurtle/BoxTurtle/tree/main/STLs/Extruder/D2HW_Switch/motor_plate_x4.stl) | 4 ☐☐☐☐
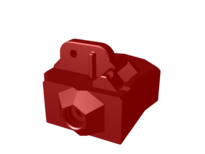
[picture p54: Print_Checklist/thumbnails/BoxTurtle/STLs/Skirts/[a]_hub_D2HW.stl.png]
 | BoxTurtle/STLs/Skirts/[a]_hub_D2HW.stl (if using a hub) (https://github.com/ArmoredTurtle/BoxTurtle/tree/main/STLs/Skirts/[a]_hub_D2HW.stl) | 1 ☐

### D2F-style switches + 5mm ball bearings

STL Preview | Filename | Quantity Needed
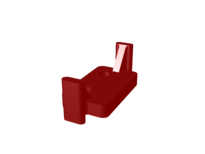
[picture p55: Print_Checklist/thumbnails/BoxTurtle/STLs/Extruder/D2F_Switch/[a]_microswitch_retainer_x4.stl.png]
 | BoxTurtle/STLs/Extruder/D2F_Switch/[a]_microswitch_retainer_x4.stl (https://github.com/ArmoredTurtle/BoxTurtle/tree/main/STLs/Extruder/D2F_Switch/[a]_microswitch_retainer_x4.stl) | 4 ☐☐☐☐
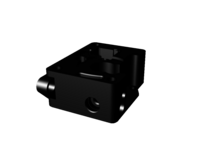
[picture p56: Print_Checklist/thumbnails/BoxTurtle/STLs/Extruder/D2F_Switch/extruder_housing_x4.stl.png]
 | BoxTurtle/STLs/Extruder/D2F_Switch/extruder_housing_x4.stl (https://github.com/ArmoredTurtle/BoxTurtle/tree/main/STLs/Extruder/D2F_Switch/extruder_housing_x4.stl) | 4 ☐☐☐☐
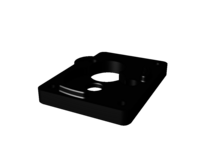
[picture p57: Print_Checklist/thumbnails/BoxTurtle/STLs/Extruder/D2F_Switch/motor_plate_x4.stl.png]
 | BoxTurtle/STLs/Extruder/D2F_Switch/motor_plate_x4.stl (https://github.com/ArmoredTurtle/BoxTurtle/tree/main/STLs/Extruder/D2F_Switch/motor_plate_x4.stl) | 4 ☐☐☐☐
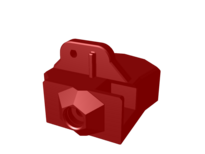
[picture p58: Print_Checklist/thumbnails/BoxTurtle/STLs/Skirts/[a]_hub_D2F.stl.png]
 | BoxTurtle/STLs/Skirts/[a]_hub_D2F.stl (if using a hub) (https://github.com/ArmoredTurtle/BoxTurtle/tree/main/STLs/Skirts/[a]_hub_D2F.stl) | 1 ☐

## Corners - print ONE set

### Corners - Printed (with LEDs)

STL Preview | Filename | Quantity Needed
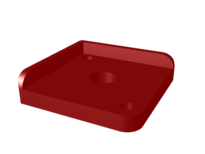
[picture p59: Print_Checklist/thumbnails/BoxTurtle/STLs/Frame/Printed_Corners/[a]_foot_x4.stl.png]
 | BoxTurtle/STLs/Frame/Printed_Corners/[a]_foot_x4.stl (https://github.com/ArmoredTurtle/BoxTurtle/tree/main/STLs/Frame/Printed_Corners/[a]_foot_x4.stl) | 4 ☐☐☐☐
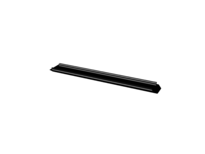
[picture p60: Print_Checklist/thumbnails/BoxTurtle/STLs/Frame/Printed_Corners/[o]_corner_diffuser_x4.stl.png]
 | BoxTurtle/STLs/Frame/Printed_Corners/[o]_corner_diffuser_x4.stl (https://github.com/ArmoredTurtle/BoxTurtle/tree/main/STLs/Frame/Printed_Corners/[o]_corner_diffuser_x4.stl) | 4 ☐☐☐☐
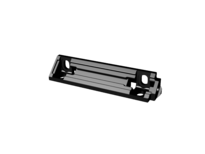
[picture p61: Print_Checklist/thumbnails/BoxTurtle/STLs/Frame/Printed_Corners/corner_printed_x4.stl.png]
 | BoxTurtle/STLs/Frame/Printed_Corners/corner_printed_x4.stl (https://github.com/ArmoredTurtle/BoxTurtle/tree/main/STLs/Frame/Printed_Corners/corner_printed_x4.stl) | 4 ☐☐☐☐
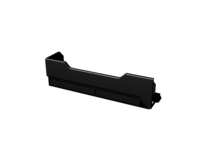
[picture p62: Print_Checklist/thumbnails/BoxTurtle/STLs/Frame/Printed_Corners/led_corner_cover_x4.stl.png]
 | BoxTurtle/STLs/Frame/Printed_Corners/led_corner_cover_x4.stl (https://github.com/ArmoredTurtle/BoxTurtle/tree/main/STLs/Frame/Printed_Corners/led_corner_cover_x4.stl) | 4 ☐☐☐☐
 | BoxTurtle/STLs/Frame/Printed_Corners/led_frame_x4.stl (https://github.com/ArmoredTurtle/BoxTurtle/tree/main/STLs/Frame/Printed_Corners/led_frame_x4.stl) | 4 ☐☐☐☐

### Corners - Printed (no LEDs)

STL Preview | Filename | Quantity Needed
 | BoxTurtle/STLs/Frame/Printed_Corners/[a]_foot_x4.stl (https://github.com/ArmoredTurtle/BoxTurtle/tree/main/STLs/Frame/Printed_Corners/[a]_foot_x4.stl) | 4 ☐☐☐☐
 | BoxTurtle/STLs/Frame/Printed_Corners/corner_printed_x4.stl (https://github.com/ArmoredTurtle/BoxTurtle/tree/main/STLs/Frame/Printed_Corners/corner_printed_x4.stl) | 4 ☐☐☐☐
 | BoxTurtle/STLs/Frame/Printed_Corners/solid_corner_cover_x4.stl (https://github.com/ArmoredTurtle/BoxTurtle/tree/main/STLs/Frame/Printed_Corners/solid_corner_cover_x4.stl) | 4 ☐☐☐☐

### 100mm 2020 extrusions (uncommon)

STL Preview | Filename | Quantity Needed
 | BoxTurtle/STLs/Frame/Extrusion_Corners/[a]_foot_extrusion_x4.stl (https://github.com/ArmoredTurtle/BoxTurtle/tree/main/STLs/Frame/Extrusion_Corners/[a]_foot_extrusion_x4.stl) | 4 ☐☐☐☐
 | BoxTurtle/STLs/Frame/Extrusion_Corners/corner_cover_extrusion_x4.stl (https://github.com/ArmoredTurtle/BoxTurtle/tree/main/STLs/Frame/Extrusion_Corners/corner_cover_extrusion_x4.stl) | 4 ☐☐☐☐
 | BoxTurtle/STLs/Frame/Extrusion_Corners/no_panel_spacer_extrusion_x4.stl (https://github.com/ArmoredTurtle/BoxTurtle/tree/main/STLs/Frame/Extrusion_Corners/no_panel_spacer_extrusion_x4.stl) | 4 ☐☐☐☐

## Rear skirts (print one, hub or passthrough)

STL Preview | Filename | Quantity Needed
 | BoxTurtle/STLs/Skirts/rear_skirt_center_hub.stl (https://github.com/ArmoredTurtle/BoxTurtle/tree/main/STLs/Skirts/rear_skirt_center_hub.stl) | 1 ☐
 | BoxTurtle/STLs/Skirts/rear_skirt_center_passthrough.stl (https://github.com/ArmoredTurtle/BoxTurtle/tree/main/STLs/Skirts/rear_skirt_center_passthrough.stl) | 1 ☐

## Trays - No Hardware (235mm or larger build plates) - print one set (if build plate allows)

### No Hardware - Desiccant

STL Preview | Filename | Quantity Needed
 | BoxTurtle/STLs/Trays_(Print_4_of_your_choice)/No_Hardware/tray_desiccant.stl (https://github.com/ArmoredTurtle/BoxTurtle/tree/main/STLs/Trays_(Print_4_of_your_choice)/No_Hardware/tray_desiccant.stl) | 4 ☐☐☐☐

### No Hardware - Inlay

STL Preview | Filename | Quantity Needed
 | BoxTurtle/STLs/Trays_(Print_4_of_your_choice)/No_Hardware/tray_inlay.stl (https://github.com/ArmoredTurtle/BoxTurtle/tree/main/STLs/Trays_(Print_4_of_your_choice)/No_Hardware/tray_inlay.stl) | 4 ☐☐☐☐
 | BoxTurtle/STLs/Trays_(Print_4_of_your_choice)/[a]_logo_inlay.stl (https://github.com/ArmoredTurtle/BoxTurtle/blob/main/STLs/Trays_(Print_4_of_your_choice)/%5Ba%5D_logo_inlay.stl) | 4 ☐☐☐☐

### No Hardware - Multicolor

STL Preview | Filename | Quantity Needed
 | BoxTurtle/STLs/Trays_(Print_4_of_your_choice)/No_Hardware/tray_multicolor.stl (https://github.com/ArmoredTurtle/BoxTurtle/tree/main/STLs/Trays_(Print_4_of_your_choice)/No_Hardware/tray_multicolor.stl) | 4 ☐☐☐☐

### No Hardware - Plain

STL Preview | Filename | Quantity Needed
 | BoxTurtle/STLs/Trays_(Print_4_of_your_choice)/No_Hardware/tray_plain.stl (https://github.com/ArmoredTurtle/BoxTurtle/tree/main/STLs/Trays_(Print_4_of_your_choice)/No_Hardware/tray_plain.stl) | 4 ☐☐☐☐

## Trays - Hardware (> 220mm but <235mm build plates) - print one set (if build plate does not allow for no hardware)

### Hardware - All

STL Preview | Filename | Quantity Needed
 | BoxTurtle/STLs/Trays_(Print_4_of_your_choice)/W_Hardware/bar_long_x4.stl (https://github.com/ArmoredTurtle/BoxTurtle/tree/main/STLs/Trays_(Print_4_of_your_choice)/W_Hardware/bar_long_x4.stl) | 4 ☐☐☐☐
 | BoxTurtle/STLs/Trays_(Print_4_of_your_choice)/W_Hardware/bar_short_x8.stl (https://github.com/ArmoredTurtle/BoxTurtle/tree/main/STLs/Trays_(Print_4_of_your_choice)/W_Hardware/bar_short_x8.stl) | 8 ☐☐☐☐☐☐☐☐

### Hardware - Desiccant

STL Preview | Filename | Quantity Needed
 | BoxTurtle/STLs/Trays_(Print_4_of_your_choice)/W_Hardware/hw_tray_desiccant.stl (https://github.com/ArmoredTurtle/BoxTurtle/tree/main/STLs/Trays_(Print_4_of_your_choice)/W_Hardware/hw_tray_desiccant.stl) | 1 ☐

### Hardware - Inlay

STL Preview | Filename | Quantity Needed
 | BoxTurtle/STLs/Trays_(Print_4_of_your_choice)/W_Hardware/hw_tray_inlay.stl (https://github.com/ArmoredTurtle/BoxTurtle/tree/main/STLs/Trays_(Print_4_of_your_choice)/W_Hardware/hw_tray_inlay.stl) | 1 ☐
 | BoxTurtle/STLs/Trays_(Print_4_of_your_choice)/[a]_logo_inlay.stl (https://github.com/ArmoredTurtle/BoxTurtle/blob/main/STLs/Trays_(Print_4_of_your_choice)/%5Ba%5D_logo_inlay.stl) | 4 ☐☐☐☐

### Hardware - Multicolor

STL Preview | Filename | Quantity Needed
 | BoxTurtle/STLs/Trays_(Print_4_of_your_choice)/W_Hardware/hw_tray_multicolor.stl (https://github.com/ArmoredTurtle/BoxTurtle/tree/main/STLs/Trays_(Print_4_of_your_choice)/W_Hardware/hw_tray_multicolor.stl) | 4 ☐☐☐☐

### Hardware - Plain

STL Preview | Filename | Quantity Needed
 | BoxTurtle/STLs/Trays_(Print_4_of_your_choice)/W_Hardware/hw_tray_plain.stl (https://github.com/ArmoredTurtle/BoxTurtle/tree/main/STLs/Trays_(Print_4_of_your_choice)/W_Hardware/hw_tray_plain.stl) | 4 ☐☐☐☐

## Desiccant Boxes (print 4 lids + 4 of one size, if using)

STL Preview | Filename | Quantity Needed
 | BoxTurtle/STLs/Trays_(Print_4_of_your_choice)/desiccant_case_18mm_x4.stl (https://github.com/ArmoredTurtle/BoxTurtle/tree/main/STLs/Trays_(Print_4_of_your_choice)/desiccant_case_18mm_x4.stl) | 4 ☐☐☐☐
 | BoxTurtle/STLs/Trays_(Print_4_of_your_choice)/desiccant_case_28mm_x4.stl (https://github.com/ArmoredTurtle/BoxTurtle/tree/main/STLs/Trays_(Print_4_of_your_choice)/desiccant_case_28mm_x4.stl) | 4 ☐☐☐☐
 | BoxTurtle/STLs/Trays_(Print_4_of_your_choice)/desiccant_lid_solid_x4.stl (print using modifier shape) (https://github.com/ArmoredTurtle/BoxTurtle/tree/main/STLs/Trays_(Print_4_of_your_choice)/desiccant_lid_solid_x4.stl) | 4 ☐☐☐☐

## Optional parts

### BoxTurtle Parts - TurtleNeck Buffer (optional)

STL Preview | Filename | Quantity Needed
 | BoxTurtle/STLs/Buffer/Frame.stl (https://github.com/ArmoredTurtle/BoxTurtle/tree/main/STLs/Buffer/Frame.stl) | 1 ☐
 | BoxTurtle/STLs/Buffer/[a]_slide.stl (https://github.com/ArmoredTurtle/BoxTurtle/tree/main/STLs/Buffer/[a]_slide.stl) | 1 ☐
 | BoxTurtle/STLs/Buffer/lid.stl (https://github.com/ArmoredTurtle/BoxTurtle/tree/main/STLs/Buffer/lid.stl) | 1 ☐

### Top-mount legs for stock Voron printers (optional) - print one set of 4 for your printer size

STL Preview | Filename | Quantity Needed
 | BoxTurtle/STLs/Mounts/turtle_leg_250_x4.stl (https://github.com/ArmoredTurtle/BoxTurtle/tree/main/STLs/Mounts/turtle_leg_250_x4.stl) | 4 ☐☐☐☐
 | BoxTurtle/STLs/Mounts/turtle_leg_300_x4.stl (https://github.com/ArmoredTurtle/BoxTurtle/tree/main/STLs/Mounts/turtle_leg_300_x4.stl) | 4 ☐☐☐☐
 | BoxTurtle/STLs/Mounts/turtle_leg_350_x4.stl (https://github.com/ArmoredTurtle/BoxTurtle/tree/main/STLs/Mounts/turtle_leg_350_x4.stl) | 4 ☐☐☐☐

## Bottom panel (optional)

STL Preview | Filename | Quantity Needed
 | BoxTurtle/STLs/Frame/bottom_panel_3mm_abs.stl (https://github.com/ArmoredTurtle/BoxTurtle/tree/main/STLs/Frame/bottom_panel_3mm_abs.stl) | 1 ☐
 | BoxTurtle/STLs/Frame/panel_spacer_x4.stl (if needed, scale in Z as appropriate) (https://github.com/ArmoredTurtle/BoxTurtle/tree/main/STLs/Frame/panel_spacer_x4.stl) | 4 ☐☐☐☐

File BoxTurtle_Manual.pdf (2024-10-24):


# BOX TURTLE

Because servos and 5.5mm ball bearings suck.

VERSION 2024-10-19

TABLE OF CONTENTS | ARMOREDTURTLE.COM

2

Introduction | 02
Build Instructions | 04

2

INTRODUCTION | ARMOREDTURTLE.COM

3

BOX TURTLE PRINTED PART GUIDELINES

3D PRINTING PROCESS
Fused Deposition Modeling (FDM)

INFILL TYPE
Gyroid

MATERIAL
ABS/ASA/PLA (no PETG)

INFILL PERCENTAGE
Recommended: 20%

LAYER HEIGHT
Recommended: 0.2mm

WALL COUNT
Recommended: 4

EXTRUSION WIDTH
Recommended: Forced 0.4mm

SOLID TOP/BOTTOM LAYERS
Recommended: 4

3

BUILD INSTRUCTIONS | ARMOREDTURTLE.COM
4 | 4

### BADGES? - PDF manual? PDF manual? WE DON’T NEED NO STINKIN’ PDF MANUAL!

### https://armoredturtle.xyz/index.html

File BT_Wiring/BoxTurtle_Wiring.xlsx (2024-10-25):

BoxTurtle Wiring
Component | Wire Length | Wire Gauge | Connector
Stepper 1 | 210mm | ? | JST-XH-4
Stepper 2 | 320mm | ? | JST-XH-4
Stepper 3 | 420mm | ? | JST-XH-4
Stepper 4 | 520mm | ? | JST-XH-4
Jumper | 80mm | 24ga | JST-XH-3/JST-SM-F
WS2812 PCB1 | 130mm/130mm tail | 24ga | JST-SM-M/JST-SM-F
WS2812 PCB2 | 130mm/130mm tail | 24ga | JST-SM-M/JST-SM-F
WS2812 PCB3 | 130mm/130mm tail | 24ga | JST-SM-M/JST-SM-F
WS28112 PCB4 | 130mm/130mm tail | 24ga | JST-SM-M/JST-SM-F
N20 6V 500RPM | 205mm | 24ga | JST-XH-2
N20 6V 500RPM | 315mm | 24ga | JST-XH-2
N20 6V 500RPM | 415mm | 24ga | JST-XH-2
N20 6V 500RPM | 515mm | 24ga | JST-XH-2
D2F-L W/Lever | 155mm | 26ga | JST-XH-3
D2F-L W/Lever | 235mm | 26ga | JST-XH-3
D2F-L W/Lever | 335mm | 26ga | JST-XH-3
D2F-L W/Lever | 435mm | 26ga | JST-XH-3
D2HW-C201 | 200mm | 26ga | JST-XH-3
D2HW-C201 | 310mm | 26ga | JST-XH-3
D2HW-C201 | 410mm | 26ga | JST-XH-3
D2HW-C201 | 465mm | 26ga | JST-XH-3 | (hub)
D2HW-C201 | 510mm | 26ga | JST-XH-3
TurtleNeck
D2F-L W/Lever | 500mm | 26ga | JST-XH-3 | (two required)

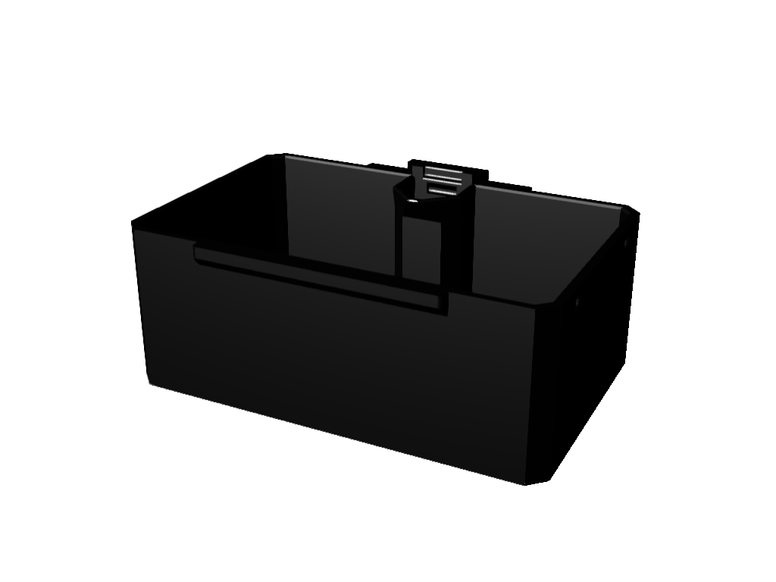
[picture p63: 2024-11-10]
Print_Checklist/images/BoxTurtle/STLs/Trays_(Print_4_of_your_choice)/desiccant_case_28mm_x4.stl.png

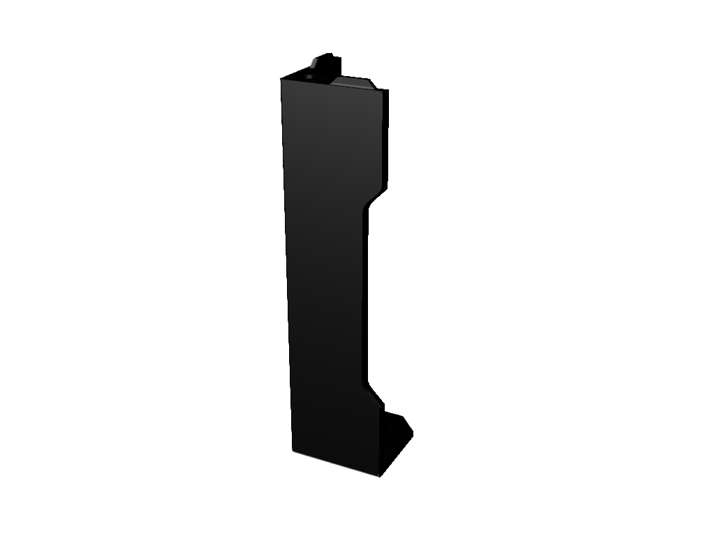
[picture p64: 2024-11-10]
Print_Checklist/images/BoxTurtle/STLs/Frame/Printed_Corners/solid_corner_cover_x4.stl.png

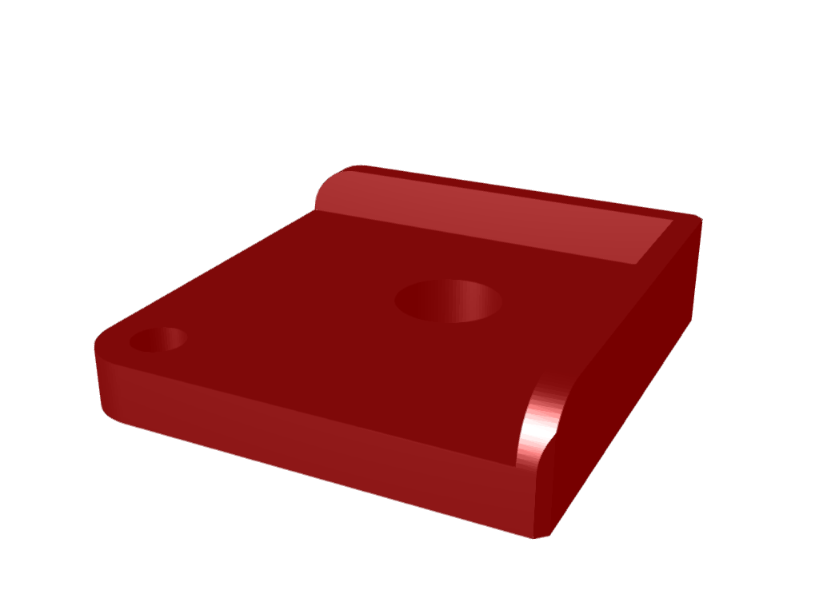
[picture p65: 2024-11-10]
Print_Checklist/images/BoxTurtle/STLs/Frame/Extrusion_Corners/[a]_foot_extrusion_x4.stl.png

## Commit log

2024-10-24 Add CAD for Open Beta
    [Box Turtle Assembled.f3z, Box Turtle Assembled.step, Box Turtle Simplified.step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]
2024-10-25 Add files via upload
    Correct JST-HX-3 to JST-XH-3
    [BoxTurtle_Wiring.xlsx]
2024-10-30 Moved logo inlay stl up a directory since it can be used in both tray types.
2024-11-01 Add print checklist
2024-11-16 Create BOM
    [BT_BOM.xlsx]
